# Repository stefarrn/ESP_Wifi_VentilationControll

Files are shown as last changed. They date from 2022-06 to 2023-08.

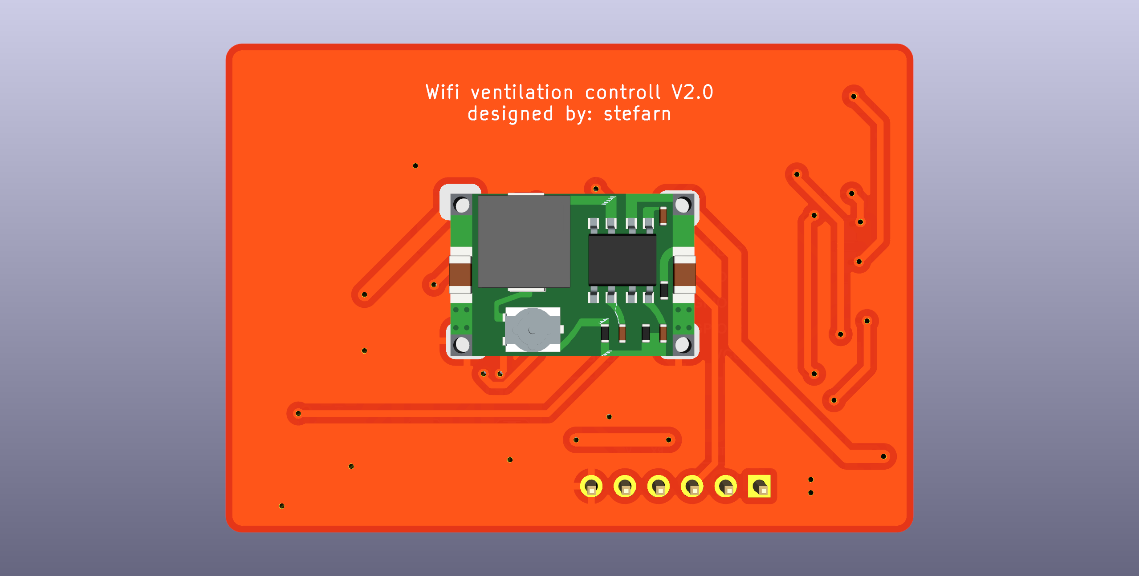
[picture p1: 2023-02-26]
Pictures/ESP_Wifi_VentilationControll_Bottom.png

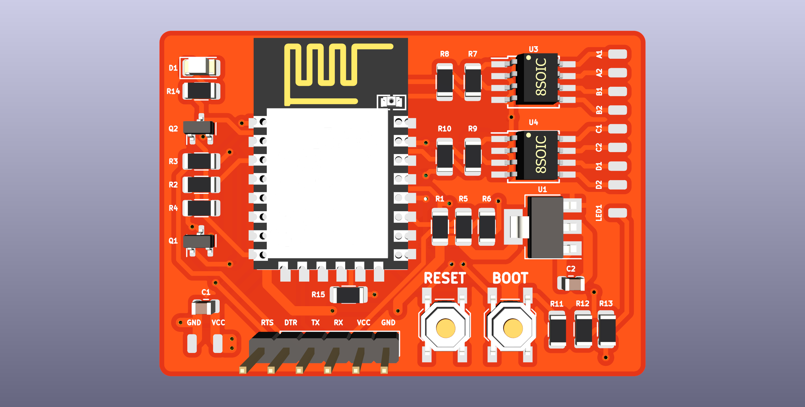
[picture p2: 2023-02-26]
Pictures/ESP_Wifi_VentilationControll.png

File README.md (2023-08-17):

# ESP_Wifi_VentilationControll
UPDATE:
after assembling the first prototype and making it work, I have applied all necessary changes to the designs and V2.0 should work straight away



modification Board in order to controll older ventilation systems over Wifi.

required tools:
1. soldering iron and solder
2. hotplate. heatgun or reflow oven for soldering the surface mount components
3. solder paste and tweezers for soldering surface mount components (ordering a stencil together with the PCBs is highly recommended)
5. computer with USB cable and USB to FTDI adapter or frog pin programmer for the ESP8266
6. Phone or tablet cabaple of running the Arduino IoT remote app
7. some prototyping cables for programming
8. multimeter or oscilocope for troubleshooting

HOW TO USE:
1. order all required parts aswell as the PCB
2. assemble the PCB acording to the schematic (make sure the buck converter is set to around 4-5 Volts before powerup)
3. flash the ESP8266 module over the Pinheader with the help of a USB to FTDI adapter (if you flashed your module before installing it this step can be skipped)
4. solder all the buttons onto pads A1 to D2, where 1 corresponds to the positive and 2 to the negative of the button
5. solder powersupply cables to the VCC and GND pads on the PCB
6. download the Arduino IoT remote app onto your device and log in with the account your ESP is connecting to (this can be done with multiple devices such that everyone can use the ventilation controller)
7. once all this is done and working you can leanback and enjoy :)

OPTIONAL:
1. if your ventilation system uses an LED to indicate wheter it is turned on or off, the pin of said LED that changes potential relative to ground can be soldered ont the LED1 pad for feedback (you might need to change the values for on and off in the software)
2. you can of course also modify the code and UI to your needs

Credits:
ESP8266 schematic symbol, footprint and 3d model by J.Dunmire 
(though I slightly modified the silkscreen on the footprint as iw was overlapping the pads)
buck converter schematic symbol, and footprint were done by me, 3d model by Wilfredo B. de los Reyes I (downloaded from grabcad.com)
schematic and PCB design by me

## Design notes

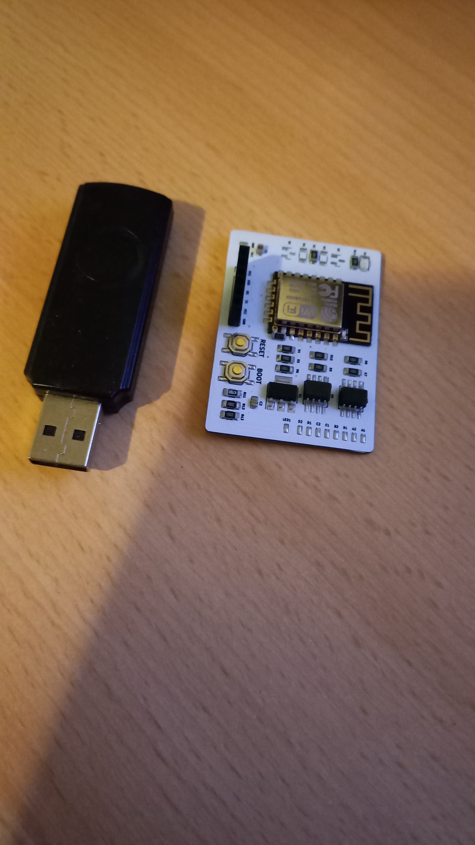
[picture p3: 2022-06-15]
Pictures/first prototype.jpg

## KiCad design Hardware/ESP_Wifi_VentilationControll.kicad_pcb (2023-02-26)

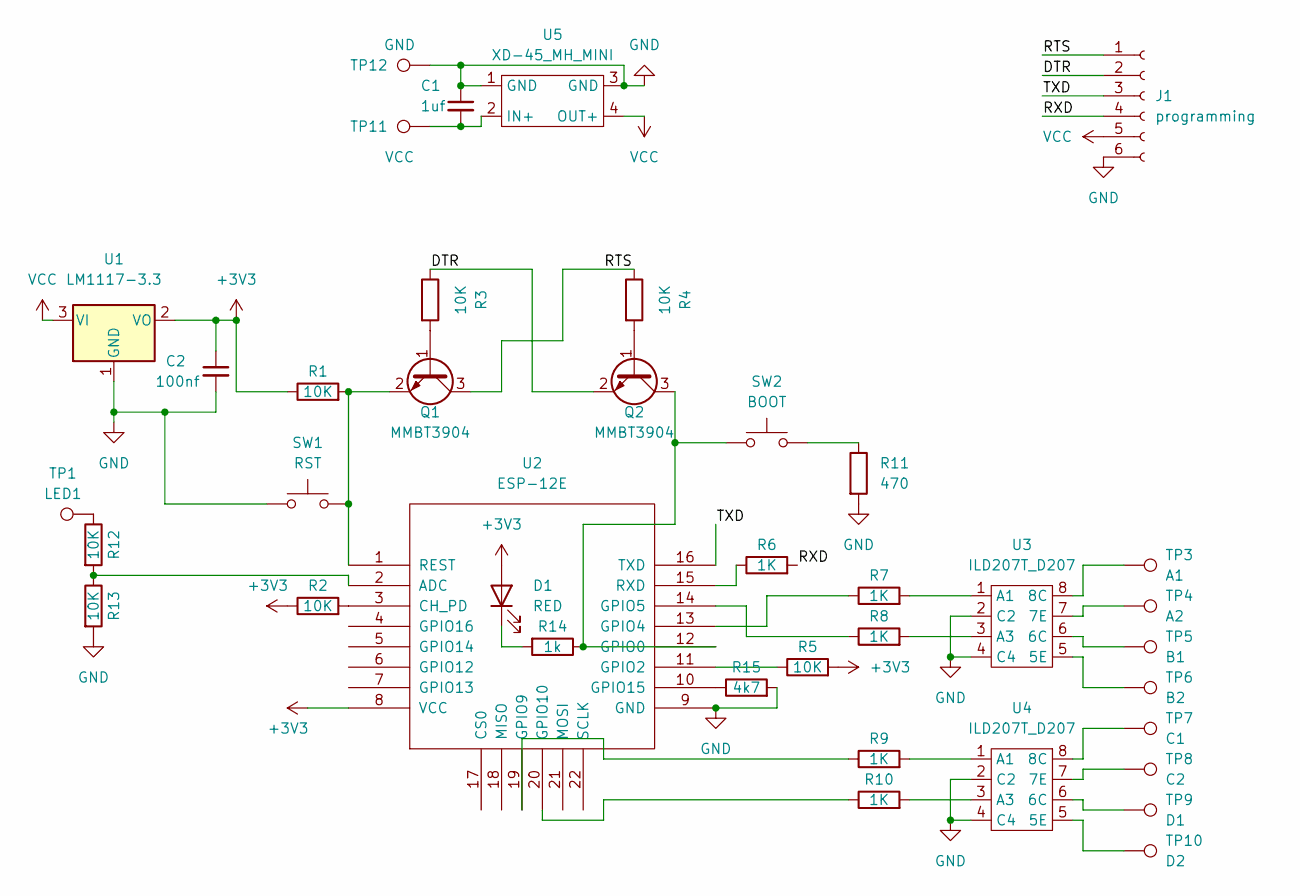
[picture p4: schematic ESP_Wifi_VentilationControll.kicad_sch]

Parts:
C1: 1uf; C_0805_2012Metric
C2: 100nf; C_0805_2012Metric
D1: RED; LED_1206_3216Metric
J1: programming; PinHeader_1x06_P2.54mm_Vertical
Q1, Q2: MMBT3904; SOT-23
R1, R2, R3, R4, R5, R12, R13: 10K; R_1206_3216Metric
R6, R7, R8, R9, R10: 1K; R_1206_3216Metric
R11: 470; R_1206_3216Metric
R14: 1k; R_1206_3216Metric
R15: 4k7; R_1206_3216Metric
SW1: RST; SW_SPST_TL3342
SW2: BOOT; SW_SPST_TL3342
TP1: LED1; SolderWirePad_1x01_SMD_1x2mm
TP3: A1; SolderWirePad_1x01_SMD_1x2mm
TP4: A2; SolderWirePad_1x01_SMD_1x2mm
TP5: B1; SolderWirePad_1x01_SMD_1x2mm
TP6: B2; SolderWirePad_1x01_SMD_1x2mm
TP7: C1; SolderWirePad_1x01_SMD_1x2mm
TP8: C2; SolderWirePad_1x01_SMD_1x2mm
TP9: D1; SolderWirePad_1x01_SMD_1x2mm
TP10: D2; SolderWirePad_1x01_SMD_1x2mm
TP11: VCC; SolderWirePad_1x01_SMD_1x2mm
TP12: GND; SolderWirePad_1x01_SMD_1x2mm
U1: LM1117-3.3; SOT-223-3_TabPin2
U2: ESP-12E; ESP-12E_SMD
U3, U4: ILD207T_D207; SOIC-8W_5.3x5.3mm_P1.27mm
U5: XD-45_MH_MINI; XD-45 MH mini

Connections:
+3V3: C2.1, D1.2 (A), R1.1, R2.1, R5.2, U1.2 (VO), U2.8 (VCC)
/DTR: J1.2, Q2.2 (E), R3.1
/RTS: J1.1, Q1.3 (C), R4.1
/RXD: J1.4, R6.2
/TXD: J1.3, U2.16 (TXD)
GND: C1.1, C2.2, J1.6, R11.2, R13.2, R15.2, SW1.1, TP12.1, U1.1 (GND), U2.9 (GND), U3.2 (C2), U3.4 (C4), U4.2 (C2), U4.4 (C4), U5.1 (GND), U5.3 (GND)
unnamed: C1.2, TP11.1, U5.2 (IN+)
unnamed: D1.1 (K), R14.2
unnamed: Q1.1 (B), R3.2
unnamed: Q1.2 (E), R1.2, SW1.2, U2.1 (REST)
unnamed: Q2.1 (B), R4.2
unnamed: Q2.3 (C), R14.1, SW2.1, U2.12 (GPIO0)
unnamed: R2.2, U2.3 (CH_PD)
unnamed: R5.1, U2.11 (GPIO2)
unnamed: R6.1, U2.15 (RXD)
unnamed: R7.1, U2.13 (GPIO4)
unnamed: R7.2, U3.1 (A1)
unnamed: R8.1, U2.14 (GPIO5)
unnamed: R8.2, U3.3 (A3)
unnamed: R9.1, U2.19 (GPIO9)
unnamed: R9.2, U4.1 (A1)
unnamed: R10.1, U2.20 (GPIO10)
unnamed: R10.2, U4.3 (A3)
unnamed: R11.1, SW2.2
unnamed: R12.1, TP1.1
unnamed: R12.2, R13.1, U2.2 (ADC)
unnamed: R15.1, U2.10 (GPIO15)
unnamed: TP3.1, U3.8 (8C)
unnamed: TP4.1, U3.7 (7E)
unnamed: TP5.1, U3.6 (6C)
unnamed: TP6.1, U3.5 (5E)
unnamed: TP7.1, U4.8 (8C)
unnamed: TP8.1, U4.7 (7E)
unnamed: TP9.1, U4.6 (6C)
unnamed: TP10.1, U4.5 (5E)
VCC: J1.5, U1.3 (VI), U5.4 (OUT+)

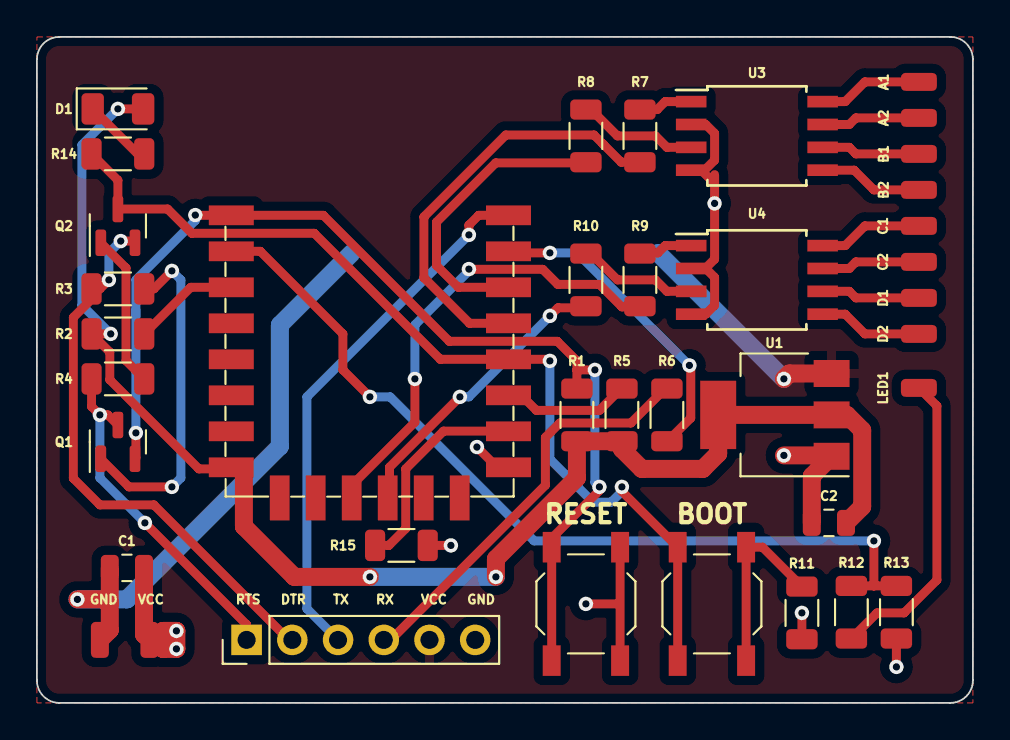
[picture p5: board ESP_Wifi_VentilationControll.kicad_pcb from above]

Board: 2 copper layers, 52.0 x 37.0 mm, 39 parts (1 on the bottom side), 36 nets.

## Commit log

2022-05-11 created schematic and PCB
    [Ventilation_controll.kicad_pcb, Ventilation_controll.kicad_sch]
2022-05-11 changed filenames
    [ESP_Wifi_VentilationControll.kicad_pcb, ESP_Wifi_VentilationControll.kicad_sch]
2022-05-11 added smoothing capacitors
    [ESP_Wifi_VentilationControll.kicad_pcb, ESP_Wifi_VentilationControll.kicad_sch]
2022-05-11 added status LED
    [ESP_Wifi_VentilationControll.kicad_pcb, ESP_Wifi_VentilationControll.kicad_sch]
2022-05-13 added librarys
    [ESP_Wifi_VentilationControll.kicad_pcb, ESP_Wifi_VentilationControll.kicad_sch]
2022-05-17 generated gerber files
    [ESP_Wifi_VentilationControll.kicad_pcb]
2022-06-09 added missing resistor values
    [ESP_Wifi_VentilationControll.kicad_sch]
2022-06-14 fixed some footprints and added missing resistor
    [ESP_Wifi_VentilationControll.kicad_pcb, ESP_Wifi_VentilationControll.kicad_sch]
2022-06-14 removed old gerber files
2022-06-15 rendered new pictures
    [ESP_Wifi_VentilationControll.kicad_pcb]
